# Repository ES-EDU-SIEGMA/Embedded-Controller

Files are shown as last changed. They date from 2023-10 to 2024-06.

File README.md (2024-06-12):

# Drink Mixing Machine Controller

This repository provides the source code for the RP2040 based stepper driver controller.
Further documentation of the hardware can be found in
the [main](https://git.uni-due.de/embedded-systems/student-projects/ss23-drink-mixing-machine/main) repository.

**The main branch of this repository can be considered stable and should be working at all time.**

## Local DEV Environment

### Toolchain

Required tools for the toolchain are:

- gcc (C-Compiler)
- arm-none-eabi-gcc (ARM C-Compiler)
- CMake (Build Script Generator)
- Ninja/Make (Build Tool)

### Build with CMake

#### Genrate Build Scripts

The build scripts can be generated by executing CMake in your Terminal as follows:

```bash
cmake -B build/<profile> -DUNIT_TEST:BOOL=<ON/OFF>  -DDEBUG:BOOL=<ON/OFF> -DCMAKE_BUILD_TYPE=<Debug/MinSizeRel>
```

The profile is one of three:

- _debug_
- _release_
- _unittest_

The `UNIT_TEST` option should be _ON_ for the unit-test profile and otherwise _OFF_.

The `DEBUG` option should be _OFF_ for the release profile and otherwise _ON_ to enable enhanced debug output.

The `CMAKE_BUILD_TYPE` option should be set to _MinSizeRel_ for the final targets to flash the machine for operations,
because otherwise the application provides too much output, that disturb the Python-based control application.

#### Build Targets

The targets to flash the Tiny2040 can be built by running

```bash
cmake --build build/<profile> -j4
```

The profile is one of three:

- _debug_
- _release_
- _unit-test_

## Contribution Guidelines

The source code should be formatted according to the style specified in the [.clang-format](.clang-format) file.

There are no direct commits to the main branch allowed.
If you want to contribute source-code, feel free to open a merge request with your desired changes.

### Folder Structure

The source code for the target device can be found under [src](src).
The [integration](test/integration) folder provides you with the integration tests which also double as an example for
the usage of the provided libraries.
The unit-tests aim to be executed on the local machine/server and are implemented under [unit](test/unit).

## Troubleshooting

### Serial Communication (Debugging)

The application detects the end of a send command by searching for _EOL_ (0x0A) or `\n`.
This character is not on the standard keyboard!
In minicom, for example, it can be sent with `CTRL+J`.

### Stepper Driver not working

Try with Arduino mega with example code from the TMC2209 library each stepper driver.
If the stepper driver is still not working, test after taking each of those steps:

- Check each connection
- Make sure TX and RX are correctly wired
- Use multiple different stepper drivers
- Use different USB cable to connect your computer
- Replace resistors
- Try with a different computer

If it works with the Arduino, the connections are all correct.
Try again with the pico.
If it does not work:

- Replace the pico
- Use different cable to connect your computer
- Use a different computer

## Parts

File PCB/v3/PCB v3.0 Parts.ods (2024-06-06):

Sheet: ORDER LIST
Part | Value | Formfactor | Required | Inventory | To Order | Seller | Part No. | Orderlink
MCU |  | TINY2040_HEADER | 5 | 0 | 5 | Digikey | 1778-PIM558-ND | https://www.digikey.de/short/qmt8ppf7
TMC Silentstepstick |  | TMC2209_SILENTSTEPSTICK | 20 | 8 | 12 | Mouser | 700-TMC2209SILENTSTE | https://www.digikey.de/short/qmt8ppf7 (https://mou.sr/486m3fp)
Base for Fuse |  | 4628 | 15 | 0 | 15 | Mouser | 534-4628 | https://mou.sr/3Nxg76M
Electronic Catridge Fuse |  | Cylindircal | 5 | 5 | 0
Motor Catridge Fuse | 35W @ 24V | Cylindircal | 5 | 5 | 0
TVS Diode 3V3 | PTVS3V3S1UR | PTVS3V3S1UR | 5 | 0 | 5 | Mouser | 771-PTVS3V3S1UR115 | https://mou.sr/3NCS0no
TVS Diode 5V0 | PTVS5V0S1UR | PTVS5V0S1UR | 5 | 0 | 5 | Mouser | 771-PTVS5V0S1UR115 | https://mou.sr/4atKc0L
TVS Diode 24V0 | PTVS24VS1UR | PTVS24VS1UR | 85 | 0 | 85 | Mouser | 771-PTVS24VS1UR115 | https://mou.sr/3xw49BO
Connector Header 2 Pin | B2B-PH-K-S(LF)(SN) | B2B-PH-K-S(LF)(SN) | 30 | 10 | 20 | Mouser | 571-292133-2 | https://mou.sr/475O9Gk
Connector Header 4 Pin | B4B-PH-K-S(LF)(SN) | B4B-PH-K-S(LF)(SN) | 30 | 10 | 20 | Mouser | 571-292133-4 | https://mou.sr/3RsRhpT
10k Ohm Resistor | 10kR | R-EU_R0805 | 25 | 25 | 0 | Mouser | 71-RCC080510K0FKEA | https://mou.sr/3R21yuH
100 Ohm Resistor | 100R +-5% | R-EU_R0805 | 5 | 5 | 0 | Mouser | 71-RCC0805100RFKEA | https://mou.sr/3RodXYk
0 Ohm Resistor | 0R | R-EU_R0805 | 25 |  | 25 | Mouser | 71-RCC08050000Z0EA | https://mou.sr/3NAsb7e

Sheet: Part List
Part | Value | Device | Package | Library
3V3_FUSE1 | 4628 | 4628 | FUSE_4628 | 4628
5V_FUSE | 4628 | 4628 | FUSE_4628 | 4628
24V_FUSE | 4628 | 4628 | FUSE_4628 | 4628
CONTROLLER | TINY2040_HEADER | TINY2040_HEADER | TINY2040_HEADER | tiny2040_headerd
D1 | PTVS3V3S1UR | PTVS3V3S1UR | TVS_PTVS3V3S1UR | PTVS3V3S1UR
D2 | PTVS5V0S1UR | PTVS5V0S1UR | TVS_PTVS5V0S1UR | PTVS5V0S1UR
D3 | PTVS24VS1UR | PTVS24VS1UR | TVS_PTVS24VS1UR | PTVS24VS1UR
D4 | PTVS24VS1UR | PTVS24VS1UR | TVS_PTVS24VS1UR | PTVS24VS1UR
D5 | PTVS24VS1UR | PTVS24VS1UR | TVS_PTVS24VS1UR | PTVS24VS1UR
D6 | PTVS24VS1UR | PTVS24VS1UR | TVS_PTVS24VS1UR | PTVS24VS1UR
D7 | PTVS24VS1UR | PTVS24VS1UR | TVS_PTVS24VS1UR | PTVS24VS1UR
D8 | PTVS24VS1UR | PTVS24VS1UR | TVS_PTVS24VS1UR | PTVS24VS1UR
D9 | PTVS24VS1UR | PTVS24VS1UR | TVS_PTVS24VS1UR | PTVS24VS1UR
D10 | PTVS24VS1UR | PTVS24VS1UR | TVS_PTVS24VS1UR | PTVS24VS1UR
D11 | PTVS24VS1UR | PTVS24VS1UR | TVS_PTVS24VS1UR | PTVS24VS1UR
D12 | PTVS24VS1UR | PTVS24VS1UR | TVS_PTVS24VS1UR | PTVS24VS1UR
D13 | PTVS24VS1UR | PTVS24VS1UR | TVS_PTVS24VS1UR | PTVS24VS1UR
D14 | PTVS24VS1UR | PTVS24VS1UR | TVS_PTVS24VS1UR | PTVS24VS1UR
D15 | PTVS24VS1UR | PTVS24VS1UR | TVS_PTVS24VS1UR | PTVS24VS1UR
D16 | PTVS24VS1UR | PTVS24VS1UR | TVS_PTVS24VS1UR | PTVS24VS1UR
D17 | PTVS24VS1UR | PTVS24VS1UR | TVS_PTVS24VS1UR | PTVS24VS1UR
D18 | PTVS24VS1UR | PTVS24VS1UR | TVS_PTVS24VS1UR | PTVS24VS1UR
D19 | PTVS24VS1UR | PTVS24VS1UR | TVS_PTVS24VS1UR | PTVS24VS1UR
LED | B2B-PH-K-S(LF)(SN) | B2B-PH-K-S(LF)(SN) | JST_B2B-PH-K-S(LF)(SN) | B2B-PH-K-S_LF__SN_
M1 | B4B-PH-K-S(LF)(SN) | B4B-PH-K-S(LF)(SN) | JST_B4B-PH-K-S(LF)(SN) | B4B-PH-K-S_LF__SN_
M1_TMC | TMC2209_SILENTSTEPSTICK | TMC2209_SILENTSTEPSTICK | MODULE_TMC2209_SILENTSTEPSTICK | TMC2209_SILENTSTEPSTICK
M2 | B4B-PH-K-S(LF)(SN) | B4B-PH-K-S(LF)(SN) | JST_B4B-PH-K-S(LF)(SN) | B4B-PH-K-S_LF__SN_
M2_TMC | TMC2209_SILENTSTEPSTICK | TMC2209_SILENTSTEPSTICK | MODULE_TMC2209_SILENTSTEPSTICK | TMC2209_SILENTSTEPSTICK
M3 | B4B-PH-K-S(LF)(SN) | B4B-PH-K-S(LF)(SN) | JST_B4B-PH-K-S(LF)(SN) | B4B-PH-K-S_LF__SN_
M3_TMC | TMC2209_SILENTSTEPSTICK | TMC2209_SILENTSTEPSTICK | MODULE_TMC2209_SILENTSTEPSTICK | TMC2209_SILENTSTEPSTICK
M4 | B4B-PH-K-S(LF)(SN) | B4B-PH-K-S(LF)(SN) | JST_B4B-PH-K-S(LF)(SN) | B4B-PH-K-S_LF__SN_
M4_TMC | TMC2209_SILENTSTEPSTICK | TMC2209_SILENTSTEPSTICK | MODULE_TMC2209_SILENTSTEPSTICK | TMC2209_SILENTSTEPSTICK
POWER_CONNECTOR | B4B-PH-K-S(LF)(SN) | B4B-PH-K-S(LF)(SN) | JST_B4B-PH-K-S(LF)(SN) | B4B-PH-K-S_LF__SN_
R1 | 10kR | R-EU_R0805 | R0805 | rcl
R2 | 10kR | R-EU_R0805 | R0805 | rcl
R3 | 10kR | R-EU_R0805 | R0805 | rcl
R4 | 10kR | R-EU_R0805 | R0805 | rcl
R5 | 10kR | R-EU_R0805 | R0805 | rcl
R6 | 100R +-5% | R-EU_R0805 | R0805 | rcl
R7 | 0R | R-EU_R0805 | R0805 | rcl
R8 | 0R | R-EU_R0805 | R0805 | rcl
R9 | 0R | R-EU_R0805 | R0805 | rcl
R10 | 0R | R-EU_R0805 | R0805 | rcl
R11 | 0R | R-EU_R0805 | R0805 | rcl
S1 | B2B-PH-K-S(LF)(SN) | B2B-PH-K-S(LF)(SN) | JST_B2B-PH-K-S(LF)(SN) | B2B-PH-K-S_LF__SN_
S2 | B2B-PH-K-S(LF)(SN) | B2B-PH-K-S(LF)(SN) | JST_B2B-PH-K-S(LF)(SN) | B2B-PH-K-S_LF__SN_
S3 | B2B-PH-K-S(LF)(SN) | B2B-PH-K-S(LF)(SN) | JST_B2B-PH-K-S(LF)(SN) | B2B-PH-K-S_LF__SN_
S4 | B2B-PH-K-S(LF)(SN) | B2B-PH-K-S(LF)(SN) | JST_B2B-PH-K-S(LF)(SN) | B2B-PH-K-S_LF__SN_
SPI_I2C | B4B-PH-K-S(LF)(SN) | B4B-PH-K-S(LF)(SN) | JST_B4B-PH-K-S(LF)(SN) | B4B-PH-K-S_LF__SN_
UART_1 | B2B-PH-K-S(LF)(SN) | B2B-PH-K-S(LF)(SN) | JST_B2B-PH-K-S(LF)(SN) | B2B-PH-K-S_LF__SN_

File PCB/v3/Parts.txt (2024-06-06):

Partlist

Exported from controller_board.sch at 06.02.24 19:13

EAGLE Version 9.6.2 Copyright (c) 1988-2020 Autodesk, Inc.

Assembly variant: 

Part            Value                   Device                  Package                        Library                 Sheet

3V3_FUSE1       4628                    4628                    FUSE_4628                      4628                    1
5V_FUSE         4628                    4628                    FUSE_4628                      4628                    1
24V_FUSE        4628                    4628                    FUSE_4628                      4628                    1
CONTROLLER      TINY2040_HEADER         TINY2040_HEADER         TINY2040_HEADER                tiny2040_headerd        1
D1              PTVS3V3S1UR             PTVS3V3S1UR             TVS_PTVS3V3S1UR                PTVS3V3S1UR             1
D2              PTVS5V0S1UR             PTVS5V0S1UR             TVS_PTVS5V0S1UR                PTVS5V0S1UR             1
D3              PTVS24VS1UR             PTVS24VS1UR             TVS_PTVS24VS1UR                PTVS24VS1UR             1
D4              PTVS24VS1UR             PTVS24VS1UR             TVS_PTVS24VS1UR                PTVS24VS1UR             1
D5              PTVS24VS1UR             PTVS24VS1UR             TVS_PTVS24VS1UR                PTVS24VS1UR             1
D6              PTVS24VS1UR             PTVS24VS1UR             TVS_PTVS24VS1UR                PTVS24VS1UR             1
D7              PTVS24VS1UR             PTVS24VS1UR             TVS_PTVS24VS1UR                PTVS24VS1UR             1
D8              PTVS24VS1UR             PTVS24VS1UR             TVS_PTVS24VS1UR                PTVS24VS1UR             1
D9              PTVS24VS1UR             PTVS24VS1UR             TVS_PTVS24VS1UR                PTVS24VS1UR             1
D10             PTVS24VS1UR             PTVS24VS1UR             TVS_PTVS24VS1UR                PTVS24VS1UR             1
D11             PTVS24VS1UR             PTVS24VS1UR             TVS_PTVS24VS1UR                PTVS24VS1UR             1
D12             PTVS24VS1UR             PTVS24VS1UR             TVS_PTVS24VS1UR                PTVS24VS1UR             1
D13             PTVS24VS1UR             PTVS24VS1UR             TVS_PTVS24VS1UR                PTVS24VS1UR             1
D14             PTVS24VS1UR             PTVS24VS1UR             TVS_PTVS24VS1UR                PTVS24VS1UR             1
D15             PTVS24VS1UR             PTVS24VS1UR             TVS_PTVS24VS1UR                PTVS24VS1UR             1
D16             PTVS24VS1UR             PTVS24VS1UR             TVS_PTVS24VS1UR                PTVS24VS1UR             1
D17             PTVS24VS1UR             PTVS24VS1UR             TVS_PTVS24VS1UR                PTVS24VS1UR             1
D18             PTVS24VS1UR             PTVS24VS1UR             TVS_PTVS24VS1UR                PTVS24VS1UR             1
D19             PTVS24VS1UR             PTVS24VS1UR             TVS_PTVS24VS1UR                PTVS24VS1UR             1
LED             B2B-PH-K-S(LF)(SN)      B2B-PH-K-S(LF)(SN)      JST_B2B-PH-K-S(LF)(SN)         B2B-PH-K-S_LF__SN_      1
M1              B4B-PH-K-S(LF)(SN)      B4B-PH-K-S(LF)(SN)      JST_B4B-PH-K-S(LF)(SN)         B4B-PH-K-S_LF__SN_      1
M1_TMC          TMC2209_SILENTSTEPSTICK TMC2209_SILENTSTEPSTICK MODULE_TMC2209_SILENTSTEPSTICK TMC2209_SILENTSTEPSTICK 1
M2              B4B-PH-K-S(LF)(SN)      B4B-PH-K-S(LF)(SN)      JST_B4B-PH-K-S(LF)(SN)         B4B-PH-K-S_LF__SN_      1
M2_TMC          TMC2209_SILENTSTEPSTICK TMC2209_SILENTSTEPSTICK MODULE_TMC2209_SILENTSTEPSTICK TMC2209_SILENTSTEPSTICK 1
M3              B4B-PH-K-S(LF)(SN)      B4B-PH-K-S(LF)(SN)      JST_B4B-PH-K-S(LF)(SN)         B4B-PH-K-S_LF__SN_      1
M3_TMC          TMC2209_SILENTSTEPSTICK TMC2209_SILENTSTEPSTICK MODULE_TMC2209_SILENTSTEPSTICK TMC2209_SILENTSTEPSTICK 1
M4              B4B-PH-K-S(LF)(SN)      B4B-PH-K-S(LF)(SN)      JST_B4B-PH-K-S(LF)(SN)         B4B-PH-K-S_LF__SN_      1
M4_TMC          TMC2209_SILENTSTEPSTICK TMC2209_SILENTSTEPSTICK MODULE_TMC2209_SILENTSTEPSTICK TMC2209_SILENTSTEPSTICK 1
POWER_CONNECTOR B4B-PH-K-S(LF)(SN)      B4B-PH-K-S(LF)(SN)      JST_B4B-PH-K-S(LF)(SN)         B4B-PH-K-S_LF__SN_      1
R1              270R                    R-EU_R0805              R0805                          rcl                     1
R2              10kR                    R-EU_R0805              R0805                          rcl                     1
R3              10kR                    R-EU_R0805              R0805                          rcl                     1
R4              10kR                    R-EU_R0805              R0805                          rcl                     1
R5              10kR                    R-EU_R0805              R0805                          rcl                     1
R6              100R +-5%               R-EU_R0805              R0805                          rcl                     1
R7              0R                      R-EU_R0805              R0805                          rcl                     1
R8              0R                      R-EU_R0805              R0805                          rcl                     1
R9              0R                      R-EU_R0805              R0805                          rcl                     1
R10             0R                      R-EU_R0805              R0805                          rcl                     1
R11             0R                      R-EU_R0805              R0805                          rcl                     1
S1              B2B-PH-K-S(LF)(SN)      B2B-PH-K-S(LF)(SN)      JST_B2B-PH-K-S(LF)(SN)         B2B-PH-K-S_LF__SN_      1
S2              B2B-PH-K-S(LF)(SN)      B2B-PH-K-S(LF)(SN)      JST_B2B-PH-K-S(LF)(SN)         B2B-PH-K-S_LF__SN_      1
S3              B2B-PH-K-S(LF)(SN)      B2B-PH-K-S(LF)(SN)      JST_B2B-PH-K-S(LF)(SN)         B2B-PH-K-S_LF__SN_      1
S4              B2B-PH-K-S(LF)(SN)      B2B-PH-K-S(LF)(SN)      JST_B2B-PH-K-S(LF)(SN)         B2B-PH-K-S_LF__SN_      1
SPI_I2C         B4B-PH-K-S(LF)(SN)      B4B-PH-K-S(LF)(SN)      JST_B4B-PH-K-S(LF)(SN)         B4B-PH-K-S_LF__SN_      1
UART_1          B2B-PH-K-S(LF)(SN)      B2B-PH-K-S(LF)(SN)      JST_B2B-PH-K-S(LF)(SN)         B2B-PH-K-S_LF__SN_      1

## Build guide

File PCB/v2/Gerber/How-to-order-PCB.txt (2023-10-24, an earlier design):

How to Order PCB

Please refer to:
https://docs.easyeda.com/en/PCB/Order-PCB

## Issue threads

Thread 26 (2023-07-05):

Mount Display in front panel

DavidFederl, 2023-07-05:
## Description

Install the newly delivered parts into the machine. This includes making an improved version of the display fixation in the front cover.

## Related User Stories

- [Cleaning](https://github.com/orgs/ES-EDU-SIEGMA/projects/1/views/1?pane=issue&itemId=29365987)
- [60 Seconds to drink](https://github.com/orgs/ES-EDU-SIEGMA/projects/1/views/1?pane=issue&itemId=29367077)
- [Improve UI](https://github.com/orgs/ES-EDU-SIEGMA/projects/1/views/1?pane=issue&itemId=29367221)

## ToDo

- [x] Build display mount brackets
- [ ] Add Perspex cover over display-controller and PI
- [x] Install Components into Front Cover of the machine

DavidFederl, 2023-11-24:
Required extra tools:
- [Gewindeeinsatz](https://www.amazon.de/Turmberg3D-L%C3%B6tkolben-Einschmelzhilfe-Gewindeeins%C3%A4tze-Einschmelzmuttern/dp/B09NYLSKPY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)
- [Einschmelzhilfe](https://www.amazon.de/Turmberg3D-L%C3%B6tkolben-Einschmelzhilfe-Gewindeeins%C3%A4tze-Einschmelzmuttern/dp/B097RR1KCB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)
- [M3 Schraubensortiment](https://www.amazon.de/joyan-Schrauben-Innensechskant-Innensechskantschrauben-Linsenkopfschrauben/dp/B09NDPH4RN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)

DavidFederl, 2024-01-22:
Only need to add cutouts to perspex cover!

Closed 2024-01-28.

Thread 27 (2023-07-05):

Replace Wireing

DavidFederl, 2023-07-05:
## Description

Replace old wires.

## Related User Stories

## ToDo

- [x] Sensors Right Side
- [x] LED Rondell
- [x] Power Connectors

DavidFederl, 2023-11-22:
- Cable for Data Transmission: [Twisted Shielded Pair](https://www.amazon.de/Flexibilit%C3%A4t-biegebest%C3%A4ndig-Schleppkette-Twisted-Pair-abgeschirmtes/dp/B0C1K9RLN6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)
- Cable for Motor: [4 Wires](https://www.amazon.de/CARLITS-Verl%C3%A4ngerungs-4x0-3mm%C2%B2-Leuchten-Streifen/dp/B08F3HTNKR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)
- Cable for sensor: [2 Wires](https://www.amazon.de/CARLITS-2x0-32mm%C2%B2-Verzinntes-Kabelanschluss-Elektrischer/dp/B088NWL5RL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)

---

We are required to order Cable with 2 wires, because we need to redo the sensor wireing and LED wireing!

DavidFederl, 2024-01-22:
WAITING FOR: female pcb connectors

DavidFederl, 2024-01-25:
Parts arrived!

Closed 2024-02-07.

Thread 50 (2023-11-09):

Prepare a draft for interfaces for dispenser/motor libs

glencoe, 2023-11-09:
What are the problems with these libs at the moment?
How should the new interfaces look like to fix these issues?
What are functions and function signatures for each of these libs?
What is the expected behaviour for these functions?

Finally discuss the draft in the group and finalize the interfaces.

HuangQing23, 2023-11-21:
Some questions from last week
1.Why we use dispenser Emergency stop?
We just use it for testing. It should not be in the public version.

2.Should motor get the time we calculate or just execute the command we preseted in the code?

3.In motor lib, function setUpEnablePin,
MOTOR_ENABLE_PINT_0-->2
MOTOR_ENABLE_PINT_1-->3
MOTOR_ENABLE_PINT_2-->6
MOTOR_ENABLE_PINT_3-->7
In the datasheet and pcb design we can see that, 2-->6 and 3-->7 is correct, but why the function still work when
MOTOR_ENABLE_PINT_0-->2
MOTOR_ENABLE_PINT_1-->3
when it should be MOTOR_ENABLE_PINT_0-->4 and MOTOR_ENABLE_PINT_1-->5?

HuangQing23, 2023-11-22:
In motor :
1.We can change motor_t --> Motor_Entity or ?
2.For these two functions 'enableMotorByPin' and 'disableMotorByPin',we can wrap these two functions into one
3.Shall we delete function'motorIsCommunicating' cause we can just use TMC2209_isSetupAndCommunicating(&motor->tmc2209) instead or we can use an explanatory variable like 'communicationState'
4.We should delete the repetitive parts of  'moveMotorUp', 'moveMotorDown', 'stopMotor'
5.Maybe we should change the names of TMC2209_moveAtVelocity, cause it's used for 'stopMotor'

In dispenser :
for 'dispenserStateCode_t dispenserGetStateCode':
1.shall we change dispenserGetStateCode-->getDispenserState
2.delete the 'else', keep the 'if' to reduce nesting

for 'dispenserEmergencyStop':
1.We should delete it in the public version

for 'resetDispenserPosition':
1.I think we should do something in the while loop to make sure if limitswitch broken then we can stop or avoid a crisis
(when we can use torque or something to get a exact position for reset,we shall delete this function or change it )

for 'dispenserSetAllToSleepState':
we better change it to 'dispenserAllInSleepState'

also for 'dispenserState_t upState(dispenser_t *dispenser)':
we should pay attention to this code segment----
if (!limitSwitchIsClosed(dispenser->limitSwitch)) {
        dispenser->stepsDone++;
    }

In rondell :
1. We can change createRondell -->setUpRondell, in view of the code in motor. And change setUpRondell -->createRondell

In left_controller library and rondell controller :
1. We should put both 'initHardware(false)' and 'establishConnectionWithController("LEFT")' out of the main function.
So we can write a function in helper that conclude both these two funtions.
(Shall we also put in the watchdog?)
2. There are different 'initDispenser' in left_controller and rondell controller , we should separate them

HuangQing23, 2023-11-22:
We should change the code in 'handleMessage' or 'if (isLineEnd(input))' to solve the situation when we want to swtich to another controller

HuangQing23, 2023-12-01:
1.Did some renaming to make the function more readable.
2.Moved the states and motorDoStep(used to be dispenserDoStep) and dispenserAllInSleepState from dispenser library to motor library and fix the headers.
3.Write a function for 'calibrated' to make sure 'initDispenser()' and 'initRondellDispenser()' is successful. But it seems better to move it to dispenser later.
4.Add a function 'isIdentifier' in helper(handleMessage) for switch to another controller, but based on some size problem it need some more changes, but it's ok if we don't enter words except 'i'.
5.Tried to change the function 'motorIsCommunicating(Motor_t *motor)' but it seems some problems happened. We can discuss it later.

HuangQing23, 2023-12-01:
Should do cleaner separations for the structure of dispenser and motor.

HuangQing23, 2023-12-01:
Due to some medical condition I delayed this commit then I clicked the wrong button which made task 49 create its own branch so I had to link the branch to this task first but it seems like my account can't solve this problem.

YULEMING, 2023-12-05:
Have you built the `left` successfully, I tried but failed on branch [refactoring the code](https://github.com/ES-EDU-SIEGMA/Embedded-Controller/tree/refactoring-the-code).

HuangQing23, 2023-12-05:
> Have you built the `left` successfully, I tried but failed on branch [refactoring the code](https://github.com/ES-EDU-SIEGMA/Embedded-Controller/tree/refactoring-the-code).

Yeah I built it without reporting an error. But I will check again.

Closed 2024-01-09.

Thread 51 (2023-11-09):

Research if TMC provides advanced functionality

DavidFederl, 2023-11-09:
Check if the TMC SilentStepKick provides additional functionality like an stop if a torque limit is reached and if multiple steps can be done with one command.

YULEMING, 2023-11-12:
We are using:
* TMC2209 V1.2 from BIGTREETECH, here is a simplified manual from BIGTREETECH: [TMC2209-V1.2-manual.pdf](https://github.com/bigtreetech/BIGTREETECH-TMC2209-V1.2/blob/master/manual/TMC2209-V1.2-manual.pdf).
* Usongshine 17HS4401 motor: See our Documentation/datasheets/[Motor-17HS4401.pdf](https://github.com/ES-EDU-SIEGMA/Documentation/blob/main/datasheets/Motor-17HS4401.pdf)

**For your convenience**
17HS4401 Electrical Specifications:
|Step Angel (deg)|Motor Length (mm)|Rated Current (A)|Phase Resistance (ohm)|Phase Inductance (mH)|Holding Torque (N.cm Min)|Detent Torque (N.cm Max)|Rotor Inertia (g.cm<sup>2</sup>)|Lead Wired (No.)|Motor Weight (g)|
|-|-|-|-|-|-|-|-|-|-|
|1.8|40|1.7|1.5|2.8|40|2.2|54|4|280|

May it helps.

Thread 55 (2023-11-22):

New implementation of time to hold top position.

kamilloo1, 2023-11-22:
Because we made measuring torque faster in [this ](https://github.com/ES-EDU-SIEGMA/Embedded-Controller/issues/41) issue, the time to hold the top position needs to be recalculated and implemented.

YULEMING, 2023-11-28:
The current `dispenser` has an attribute `haltSteps`. It is used in topState to control the time that the dispenser stops at the top position. Because we are going to use time instead of steps, I recommend that we change `haltSteps` to `haltTime`, which means: *This dispenser is going to stop at the top position for 'haltTime' ms*. But this will influence some other dispenser functions. Details are as follows:
### File: [dispenser.h](https://github.com/ES-EDU-SIEGMA/Embedded-Controller/blob/main/src/dispenser/dispenser.h#L36)
```c
struct dispenser {
    ...
    // uint16_t haltSteps;
    uint32_t haltTime;
    ...
};
```
### File: [dispenser.c](https://github.com/ES-EDU-SIEGMA/Embedded-Controller/blob/main/src/dispenser/dispenser.c)
```c
void dispenserSetHaltTime(dispenser_t *dispenser, uint32_t haltTime) {
//    dispenser->haltSteps = haltTime / DISPENSER_STEP_TIME_MS;
    // Change dispenser->haltSteps to dispenser->haltTime
    dispenser->haltTime = haltTime;
    // PRINT_DEBUG("Dispenser %u will stop after %hu steps", dispenser->address, dispenser->haltSteps)
}
```
```c
void dispenserCreate(dispenser_t *dispenser, SerialAddress_t address, serialUart_t uart,
                     uint8_t dispenserCL, uint16_t searchTimeout) {
    ...
    // dispenser->haltSteps = 0;
    dispenser->haltTime = 0;
    ...
}
```
```c
void dispenserEmergencyStop(dispenser_t *dispenser) {
    ...
    // dispenser->haltSteps = 0;
    dispenserSetHaltTime(dispenser, 0);
    ...
}
```
* `haltTime` would be assigned every time when it needs to work, but it would be stable if we set it to 0. E.g. what if we say: *Let all dispensers start to work as long as its `haltTime` is not 0?* But that dispenser stopped last time without setting `haltTime` to 0?
```c
static dispenserState_t errorState(dispenser_t *dispenser) {
    ...
    if (...)) {
        ...
        // dispenser->haltSteps = 0;
        dispenserSetHaltTime(dispenser, 0);
        ...
    }
    ...
}
```
```c
static dispenserState_t sleepState(dispenser_t *dispenser) {
//    if (dispenser->haltSteps > 0) {
//        enableMotorByPin(&dispenser->motor);
//        moveMotorUp(&dispenser->motor);
//        return upState_t;
//    }
    return sleepState_t;
}
```
* This `sleepState` will check whether the dispenser really finished or not by checking `haltSteps`. Because we use `haltTime` instead of `haltSteps`, I don't see any situation once we get into `sleepState` but the dispenser still has unfinished steps and needs to go back to `upState`. No need to do it anymore.
```c
static dispenserState_t topState(dispenser_t *dispenser) {
    PRINT_DEBUG("topState")
    // Change dispenser->haltSteps to dispenser->haltTime
    sleep_ms(dispenser->haltTime);
    dispenserSetHaltTime(dispenser, 0);
    return downState_t;
}
```
```c
static dispenserState_t downState(dispenser_t *dispenser) {
    ...
    if (...)) {
        ...
        // dispenser->haltSteps = 0;
        dispenserSetHaltTime(dispenser, 0);
        ...
    }
    ...
}
```

YULEMING, 2023-11-28:
The current `dispenser` also has attributes `stepsUp` and `stepsDown`. Because of the above changes, these two are only working as counters. We don't do any `if condition` stuff on them. We can also get rid of them.
### File: dispenser.h
```c
struct dispenser {
    ...
    // uint16_t stepsDone;
    // uint16_t stepsUp;
    // This haltSteps is used in topState, we can change it to "haltTime"
    // uint16_t haltSteps;
    uint32_t haltTime;
    ...
};
```
### File: dispenser.c
```c
void dispenserCreate(dispenser_t *dispenser, SerialAddress_t address, serialUart_t uart,
                     uint8_t dispenserCL, uint16_t searchTimeout) {
    ...
    // This haltSteps is used in topState, we can change it to "haltTime"
    // dispenser->haltSteps = 0;
    dispenser->haltTime = 0;
    // dispenser->stepsDone = 0;
    ...
}
```
```c
static dispenserState_t upState(dispenser_t *dispenser) {
    ...
    // If the torque is below 10 twice in a row, stop
    if (torque < 10){
        ...
        if (counterTorque == 2){
            ...
            // dispenser->stepsUp = dispenser->stepsDone;
            ...
        }
    }
    else ...

    if (!limitSwitchIsClosed(dispenser->limitSwitch)) {
        // dispenser->stepsDone++;
    }
    ...
}
```
```c
static dispenserState_t downState(dispenser_t *dispenser) {
    ...
    if (limitSwitchIsClosed(dispenser->limitSwitch)) {
        ...
        // dispenser->haltSteps = 0;
        dispenserSetHaltTime(dispenser, 0);
        ...
    }
    // dispenser->stepsDone++;
    ...
}
```

glencoe, 2023-11-29:
Seems reasonable. Please open a pull request that features your changes

YULEMING, 2023-12-05:
Some problems are found with the above method, and this should be continued based on the newly refactored code.

YULEMING, 2023-12-16:
Based on `develop` branch.
```c
static dispenserState_t topState(dispenser_t *dispenser) {
    PRINT_DEBUG("topState")
    if (dispenser->haltTime > 0) {
        sleep_ms(TOP_TIME_SLOT);
        dispenser->haltTime = dispenser->haltTime - TOP_TIME_SLOT;
        return topState_t;
    }
    // reset to 0 when change to down state.
    dispenserSetHaltTime(dispenser, 0);
    moveMotorDown(&dispenser->motor);
    return downState_t;
}
```
The `TOP_TIME_SLOT` is defined as 1. Assume command `100;\n` is sent. Dispenser will sleep 1ms at the top position 100 times. If dispenser sleeps 100ms at the top position 1 time, others will have to wait 100ms.
```c
static dispenserState_t sleepState(dispenser_t *dispenser) {
    if (dispenser->haltTime > 0) {
        enableMotorByPin(&dispenser->motor);
        moveMotorUp(&dispenser->motor);
        return upState_t;
    }
    return sleepState_t;
}
```
`sleepState` will check `haltTime` instead of `haltSteps`.

#### When the refactoring is finished, I will implement the changes in new code.

YULEMING, 2024-01-15:
Make sense. Thank you for telling me that.
1. When I was doing the task: measure the torque more frequently, there was a situation that when all 4 dispensers are working, when no sleep in the end of `TMC2209_read`, 2 of 4 dispensers won't stop correctly. They stuck in the `upState`. But it worked well when 1 dispenser is working. According to how you sovled your #56, I think the reason is:
```c
static uint8_t counterTorque = 0;
static uint16_t torque = 0;
...
static dispenserState_t upState(dispenser_t *dispenser) {
    torque = motorGetTorque(dispenser->address);
    PRINT_DEBUG("upState")
    PRINT_DEBUG("Torque: %i", torque)

    // If the torque is below 10 twice in a row, stop
    if (torque < 10){
        counterTorque++;
        if (counterTorque == 2){
            PRINT_DEBUG("detect Top Position")
            stopMotor(dispenser->address);
            counterTorque = 0;
            return topState_t;
        }
    }
    else counterTorque = 0;
    return upState_t;
}
```
the `torque` here is a shared variable because we are using if statement. So the last counted torque is from another dispenser. I will try to make `torque` be non-shared and try to remove the `sleep` in the end of `TMC2209_read` to **reduce the cycle time**. Even if it has no influence on the cycle time, I still don't think it's a good idea to make `torque` here be shared.

2. I will measure the cycle time, figure out the relation between the input and real time, and adjust the sleep time in `topState`

YULEMING, 2024-01-15:
In the old `topState`, no sleep, only count halt steps. It's like: 1000 / 100 = 10 halt steps in total. Then just run `topState` 10 times. When I do `sleep` stuff, I have to consider other dispensers. Because 1 dispenser sleeps, it has to wait others to sleep. I think that's why there is a `othersTriggered` in the old `topState`. I think we do need an attribute to let the current dispenser know how many dispensers are working at the same time, and to reduce correct time or steps in one `topState`.

YULEMING, 2024-01-15:
Before one dispenser really runs one of the `xxxState` functions, it will still check the motor, which already spent 1ms. Same on topState. I saw the new downState function, there will be 1 or 2 times `motorGetTorque`. Tomorrow I will try to reduce the 1ms sleep at first. If we can't, here is my new thought:
1. use a shared counter variable declared in dispenser.h, so that it can be reset in the controller file and can be accessed in the dispenser.c file
2. reset in the beginning of every `do while` loop in controller file
3. after each `motorGetTorque`, counter++, so that we know how many 1ms already spent, in order to reduce the halt counter in `topState`.

YULEMING, 2024-02-19:
Find the proper method to implement the timing for topstate. #76
After fixing #84

YULEMING, 2024-02-27:
#### Important changes:
* @HuangQing23 moved motor check out of and before the do-while loop
* Running sequence in topState changed from:
    * motor check
    * dispenser run
    * motor check
    * dispenser run
    * motor check
    * dispenser run
    * motor check
    * dispenser run
* To: (motor check is done before going into this running sequence)
    * dispenser run
    * dispenser run
    * dispenser run
    * dispenser run
#### Based on the above changes
* The countdown method (without sleep): countdown by the number of dispensers now in topState from 1000 (number from the command) to 0,
    * approximate to 1000ms
    * the longer the halt time, the more significant the deviation
But in my point of view, the longest halt time should be the time that the dispenser need from full to empty. Longer halt time makes no or less sense.

YULEMING, 2024-02-27:
### Attention
* Please note that the same code spends different times in the `debug` and `release` modes because the `PRINT_DEBUG` stuff won't be counted in `release` mode.
* If the halt time is longer than the command, and there is `PRINT_DEBUG` or something like that, remove or comment relevant statement.

Closed 2024-02-28.

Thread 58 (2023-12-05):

Improve Unit Test Coverage

YULEMING, 2023-12-05:
* [x] Repair Unit Test. Fix bugs and build it successfully.
* [x] Figure out the current coverage of Unit Test.
* [ ] Extent the coverage of Unit Test.

YULEMING, 2023-12-11:
#### Repair Unit Test. Fix bugs and build it successfully.
* After fixing some naming and declaration errors, the unit-test can be built successfully now.
#### Figure out the current coverage of Unit Test.
It tests:
* dispenser
  * the structure of the dispenser (working)
  * the cycle of the dispenser (not working)

YULEMING, 2023-12-11:
### Extent the coverage of Unit Test.
Tasks list, from bottom to top, easy to hard:
* [ ] Limit switch
* [ ] Hardware helper
* [ ] serial UART
* [ ] tmc2209
* [ ] motor
* [ ] dispenser
* [ ] Rondell
* [ ] controller
* [ ] rondell controller

YULEMING, 2023-12-17:
Yes, just pushed [here](https://github.com/ES-EDU-SIEGMA/Embedded-Controller/tree/%2358-fix-improve-unit-test). But it's not finished yet. The CMakeLists.txt will keep changing and may not be able to be built directly.

DavidFederl, 2024-02-13:
Please see #81

Closed 2024-02-19.

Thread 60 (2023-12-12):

Create Gerber Files for PCB

DavidFederl, 2023-12-12:
Generate Gerber Files for new PCB design.

---

- [x] Determine required CAM configuration
- [x] Create all required Gerber files
- [x] Check if Gerber Files are valid!
- [x] Add Gerber Files to Repository (zip-archive)

DavidFederl, 2023-12-12:
CAM Files for JLCPCB can be downloaded from their [website](https://jlcpcb.com/help/article/9-How-to-Generate-Gerber-and-Drill-Files-in-Autodesk-Eagle).

---

To assure the gerber files are valid it is recommended to check them with a tool online tool like[gerblook](https://gerblook.org) or a local program like [gerbv](https://gerbv.github.io/).

Closed 2023-12-12.

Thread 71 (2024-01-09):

Assemble new PCBs

DavidFederl, 2024-01-09:
Assemble three new PCBs for the machine once all required components are delivered!

## ToDo

- PCB **LEFT**
    - [x] Assembled
    - [x] Integrated
    - [x] Tested
 - PCB **RIGHT**
    - [x] Assembled
    - [x] Integrated
    - [x] Tested
  - PCB **RONDELL**
    - [x] Assembled
    - [x] Integrated
    - [x] Tested

DavidFederl, 2024-01-22:
@YULEMING and @HuangQing23: I tested your PCBs -> one of them has faulty TVS-Diodes (I fixed them)

---

You only need to add the female headers for the TMC/Tiny modules. I would recommend using a broken TMC/Tiny to hold them in place while soldering.

YULEMING, 2024-02-02:
* With the new PCB board, it stops in the while loop:
```c
void setUpMotor(Motor_t *motor, SerialAddress_t address) {

    TMC2209_setupByMotor(&motor->tmc2209,address);

    while (!TMC2209_isSetupAndCommunicating(&motor->tmc2209)) {
        if (TMC2209_disabledByInputPin(&motor->tmc2209)) {
            PRINT_DEBUG("Setup: Stepper driver with address %u DISABLED by input pin!", address)
        }
        PRINT_DEBUG("Setup: Stepper driver with address %u NOT communicating and setup!", address)
        TMC2209_setupByMotor(&motor->tmc2209,address);
        sleep_ms(500);
    }
    ...
}
```
with this output:
`[MOTOR: setUpMotor] Setup: Stepper driver with address 0 NOT communicating and setup!.`
**The problem is there is something wrong when writing or reading register `GlobalConfig`**
**The `pdn_disable` bit is 1 in the message we write into the register, but is 0 when we read.**
* The condition of the while loop is checking register `GlobalConfig`:
```c
const static uint8_t ADDRESS_GCONF = 0x00;
typedef union GlobalConfig {
    struct {
        ...
        uint32_t pdn_disable : 1;
        ...
    };
    uint32_t bytes;
} TMC2209_GlobalConfig_t;
```
the `pdn_disable` bit. The while loop is done when this bit is `1`.
* We write this bit here:
```c
void setUpMotor(Motor_t *motor, SerialAddress_t address) {

    TMC2209_setupByMotor(&motor->tmc2209,address);

    ...
}
```
And we check `pdn_disable` right after `TMC2209_setupByMotor(...);`:
```c
void setUpMotor(Motor_t *motor, SerialAddress_t address) {

    TMC2209_setupByMotor(&motor->tmc2209,address);

    while (!TMC2209_isSetupAndCommunicating(&motor->tmc2209)) {
        ...
    }
    ...
}
```
* If `pdn_disable` is not `1`, we setup it again:
```c
void setUpMotor(Motor_t *motor, SerialAddress_t address) {

    TMC2209_setupByMotor(&motor->tmc2209,address);

    while (!TMC2209_isSetupAndCommunicating(&motor->tmc2209)) {
        ...
        TMC2209_setupByMotor(&motor->tmc2209,address);
        ...
    }
    ...
}
```
* The tmc setup `GlobalConfig` by calling `TMC2209_setOperationModeToSerial` inside `TMC2209_setup`:
```c
void TMC2209_setOperationModeToSerial(TMC2209_t *tmc2209, serialUart_t serial,
                                      long serial_baud_rate, SerialAddress_t serial_address) {
    ...
    tmc2209->global_config.pdn_disable = 1;
    ...

    TMC2209_writeStoredGlobalConfig(tmc2209);
}
```
as you can see `pdn_disable` is 1.
* Here we read the value of `pdn_disable`
```c
bool TMC2209_serialOperationMode(TMC2209_t *tmc2209) {
    TMC2209_GlobalConfig_t global_config;
    global_config.bytes = TMC2209_readGlobalConfigBytes(tmc2209);

    return global_config.pdn_disable;
}
```
the `global_config.pdn_disable` is returned again:
```c
bool TMC2209_isSetupAndCommunicating(TMC2209_t *tmc2209) {
    return TMC2209_serialOperationMode(tmc2209);
}
```
you can find it's 0 when you print the debug message.
All the `read` and `write` here are finally executed by `TMC2209_read` and `TMC2209_write`. If they worked well in the past, then there is nothing wrong with them?

* I tested the integration test of the limit switch and motor. When testing the limit switch, there is no change when I open or close the limit switch. When testing the motor, it also stops in the same while loop.

###Do you have any idea that anything might influence this?
* The new design of the PCB?
* The tmc is broken?
* The change of the enable pin in the code?
* Or something is wrong with the code, but somehow they still worked in the past?

YULEMING, 2024-02-02:
The PCB board with `1A` and `2A` labels, when testing the limit switch, no change when I close and open the limit switch.
The PCB board on the machine, all limit switches work well. The state of limit switch changed when I open and close them.
The rest PCB board, limit switch 1 and 2 work well. The limit switch 3 no state change. When I close and open limit switch 4, the states of limit switch 3 and 4 change together.
But all TMCs are not working on all 3 PCB boards.

DavidFederl, 2024-02-05:
The limitswitches are working as expected now. The TMC2209 are still not reachable. I'll try to figure it out, by checking the UART communication.

DavidFederl, 2024-02-06:
I would think the TMC2209 requires some form of adjustment to work properly. -> [FAQ for Setup](https://learn.watterott.com/de/silentstepstick/faq/#wie-stellt-man-den-motorstrom-ein)

DavidFederl, 2024-02-07:
> The limitswitches are working as expected now. The TMC2209 are still not reachable. I'll try to figure it out, by checking the UART communication.

The UART communication is working now. The resistor value was specified to large. It has to be 270Ω.

Closed 2024-02-07.

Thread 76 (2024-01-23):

Figure out 2 ways to implement the top timing

YULEMING, 2024-01-23:
1. Fix the shared variable `torque` in `upState` and try to reduce the sleep time in `TMC2209_read`.
2. If yes, implement the following:
3. Sample:
    1. INPUT: 1000;0;2000;3000; Assume each `topState` spend 1ms (in total, not really sleep 1ms in `topState`)
    2. OUTPUT:
        1. dispenser 1: 333 times run `topState`
        2. dispenser 2: 0
        3. dispenser 3: 333 + 500 times run `topState`
        4. dispenser 4: 333 + 500 + 1000 times run `topState`
4. Sample:
    1. INPUT: 1000;0;2000;2000;
    2. OUTPUT:
        1. dispenser 1: 333
        2. dispenser 2: 0
        3. dispenser 3: 333 + 500
        4. dispenser 4: 333 + 500
 5. If not, try interrupt.

YULEMING, 2024-01-23:
By changing torque to dispenser->torque, now the sleep time in TMC2209_read is 20us (>20us also works). 10us doesn't work at all, it can't even finish the initialization stage. I think the time influence of `motor-check` and `getTorque` stuff can be ignored.

YULEMING, 2024-02-04:
Method 3, TODOs:
1. remove sleep in topState and test the time consumption of topState.
2. use a common variable to let dispenser working in topState make a proper countdown.
3. then add sleep with proper time to let dispenser halt for a certain time.

Closed 2024-02-19.

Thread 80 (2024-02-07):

adjust TMC2209 to perform correctly

DavidFederl, 2024-02-07:
> I would think the TMC2209 requires some form of adjustment to work properly. -> [FAQ for Setup](https://learn.watterott.com/de/silentstepstick/faq/#wie-stellt-man-den-motorstrom-ein)

 _Originally posted by @DavidFederl in [#71](https://github.com/ES-EDU-SIEGMA/Embedded-Controller/issues/71#issuecomment-1930438760)_

YULEMING, 2024-02-07:
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

So the `A` and `B` of the motor are like this, but I don't know which one is A or B on the motor.
But the motor 04 on the `Left` is working well, so I moved it's connector from `M4` to `M1` and it also worked well.
The `M4` is closer to the TINY than `M1`, so I moved the connector of motor 01 from `M1` to `M4` but it still didn't work well. In this case, the cables' order is the same as motor 04.
Then I changed the order of the colored cables but none of them worked as well as motor 04.

I also exchanged the position of TMC2209 of `M4` and `M1`, but it also didn't work.

On the TMC2209 there are A1 and A2, I'm also not sure which one is A.

Might this have anything to do with the problem now on TMC2209?

DavidFederl, 2024-02-07:
The A B coils of the motor are provided with a current through the TMC2209. This current is generated by a PWM so that the motor is running smoothly.
To my point of view the TMC2209 needs to be adjusted so that the output current is set correct, like mentioned [in this guide](https://learn.watterott.com/de/silentstepstick/faq/#wie-stellt-man-den-motorstrom-ein). I would checking this by comparing a TMC2209 that is working correctly and comparing it to one not working.

DavidFederl, 2024-02-09:
Measure the current between GND and V_Ref Pin on a working TMC2209 and compare it to the non working TMC2209. If there is a difference adjust the Potentiometer to get the value measured on the working TMC2209.

DavidFederl, 2024-02-13:
# The hardware is now working as expected.

## Fixed Problems

- The tiny2040 were flashed with the wrong version of the integration test. => **Build from develop branch for now!**
- The Crimp contacts for one the motor cables failed which caused problems. => **Replaced the faulty parts**

Closed 2024-02-13.

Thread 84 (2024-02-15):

Fix the problem when testing left/rondell/right

HuangQing23, 2024-02-15:
When we use USB to connect three pcb boards to test left/rondell/right, it always stops at the execution to output  "moveDown" in 'PRINT_DEBUG("moveDown")' of 'resetDispenserPosition(dispenser_t *dispenser)'. Function 'moveMotorDown' was executed but it seems like the motors are not running.

YULEMING, 2024-02-19:
* Yes, and by integrationTest_Motor it calls the same function `moveMotorDown` but it works.
Due to it doesn't work in `resetDispenserPosition` `debug` `left`, it sticks in the following while loop:
```c
static void resetDispenserPosition(dispenser_t *dispenser) {
    ...
    moveMotorDown(dispenser->address);
    PRINT_DEBUG("moveDown")
    while (!limitSwitchIsClosed(dispenser->limitSwitch))
        ;
    ...
```
* So the question is: why `moveMotorDown` works in `integrationTest_motor` `debug`, but not in `resetDispenserPosition` `debug` `left`?
* I don't think `moveMotorUp` and `stopMotor` will either work in `resetDispenserPosition` `debug` `left`.

HuangQing23, 2024-02-20:
fix the problem by #85

HuangQing23, 2024-02-20:
To make the motors work  properly, we should get the rope wrapped clockwise around the motor's rotating shaft. This is because our function 'moveMotorDowm' will make the motor shaft rotates clockwise. If the rope is wrapped in the opposite direction of the motor shaft rotation due to rope length or over-rotation of the shaft, then the input command will rotate in the opposite direction of the actual rotation.

Closed 2024-02-21.

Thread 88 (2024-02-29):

Pass velocity for motor to setUp function

kamilloo1, 2024-02-29:
Because the rotation of the rondell requires a slower speed then the moving up of the lever of the dispenser, we need the motors to operate at two different speeds. The Dispenser requires a higher speed to make the torque detection work.
**Right now the velocity to the motor is passed via `#define` which affects the motor speed for all use cases.** To solve the problem, the velocity for the motor should be set via variables during setUp and stored inside the struct that holds the motor configuration!

DavidFederl, 2024-06-10:
See #102

Closed 2024-06-10.

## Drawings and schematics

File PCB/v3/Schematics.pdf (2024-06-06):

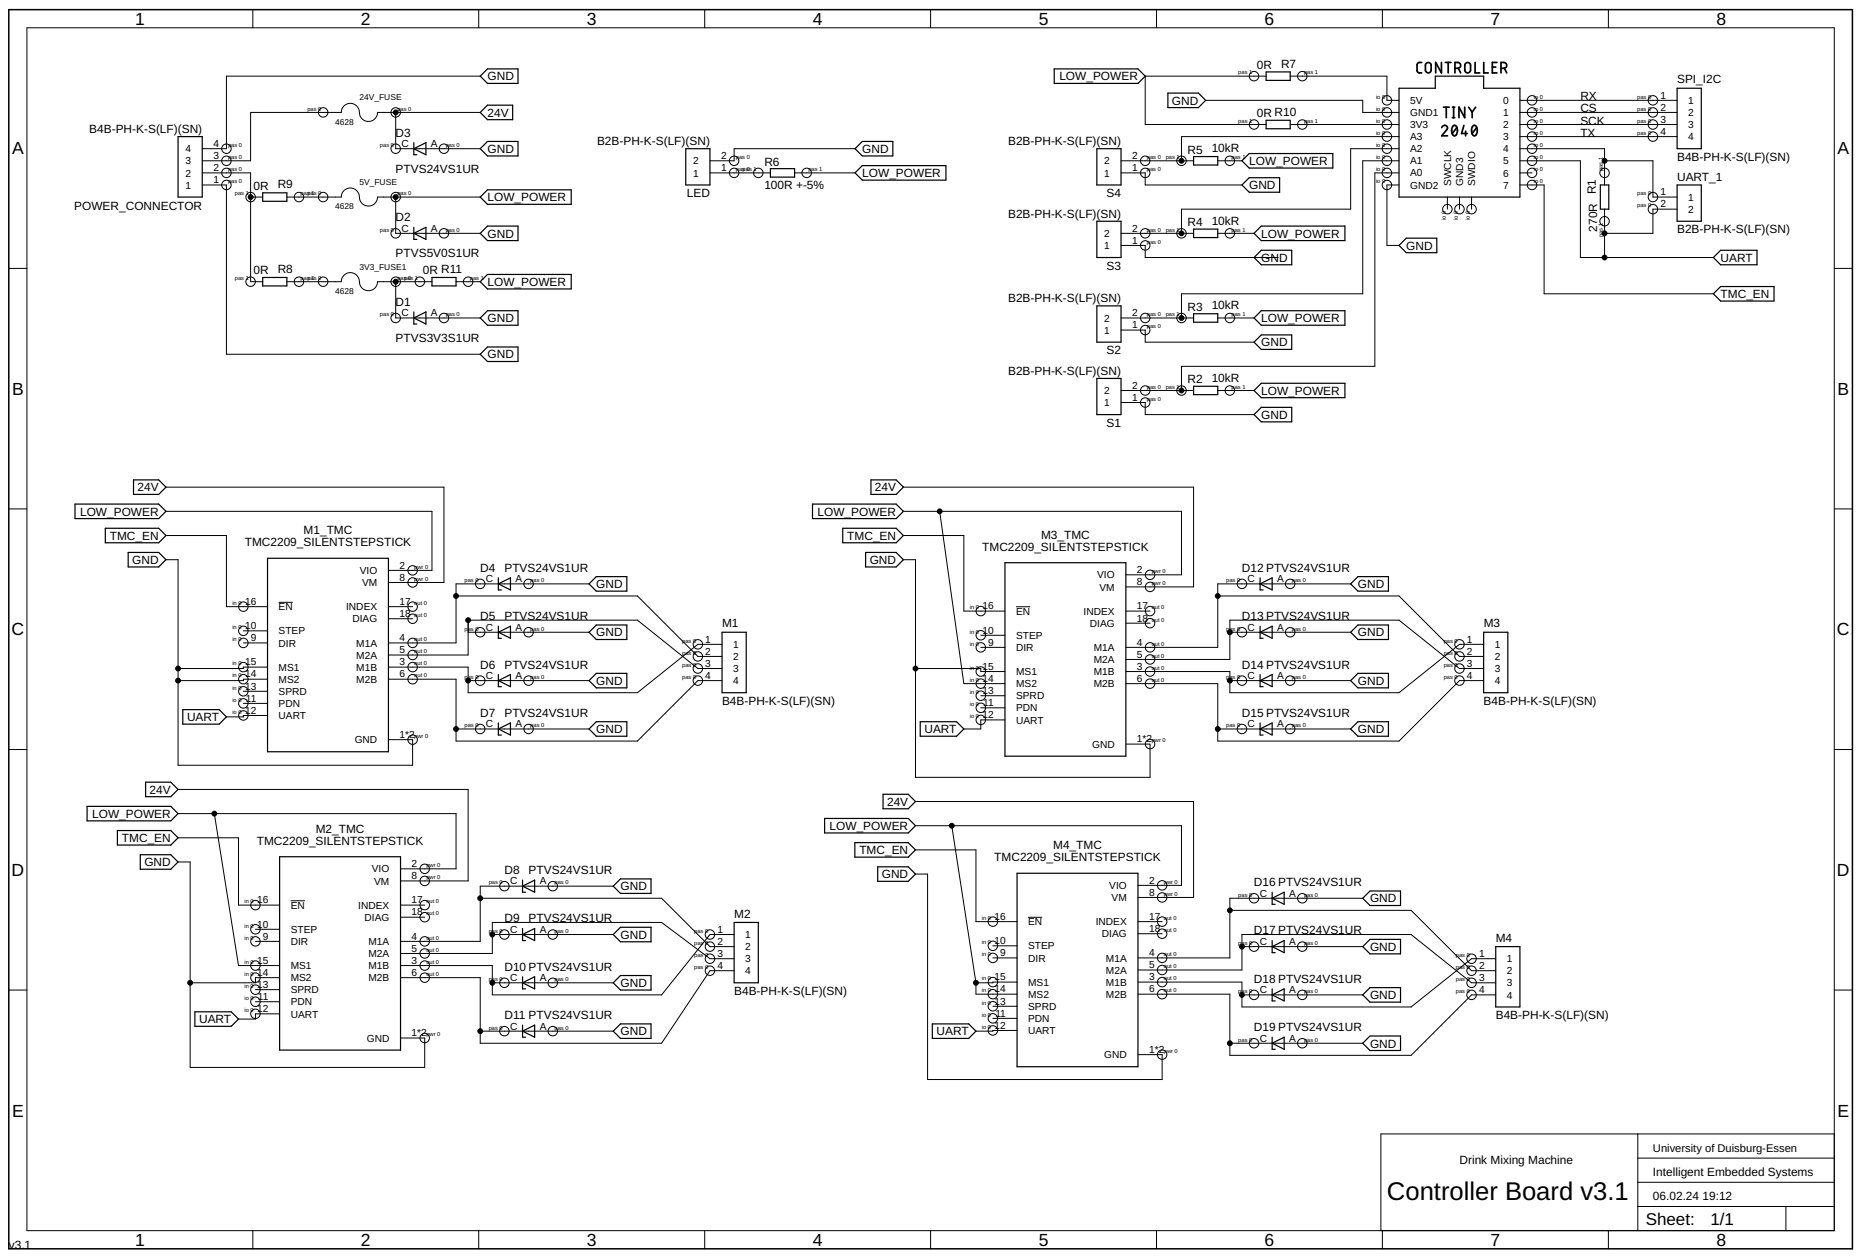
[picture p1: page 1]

Intelligent Embedded Systems University of Duisburg-Essen 06.02.24 19:12

Drink Mixing Machine Controller Board v3.1

Sheet: 1/1

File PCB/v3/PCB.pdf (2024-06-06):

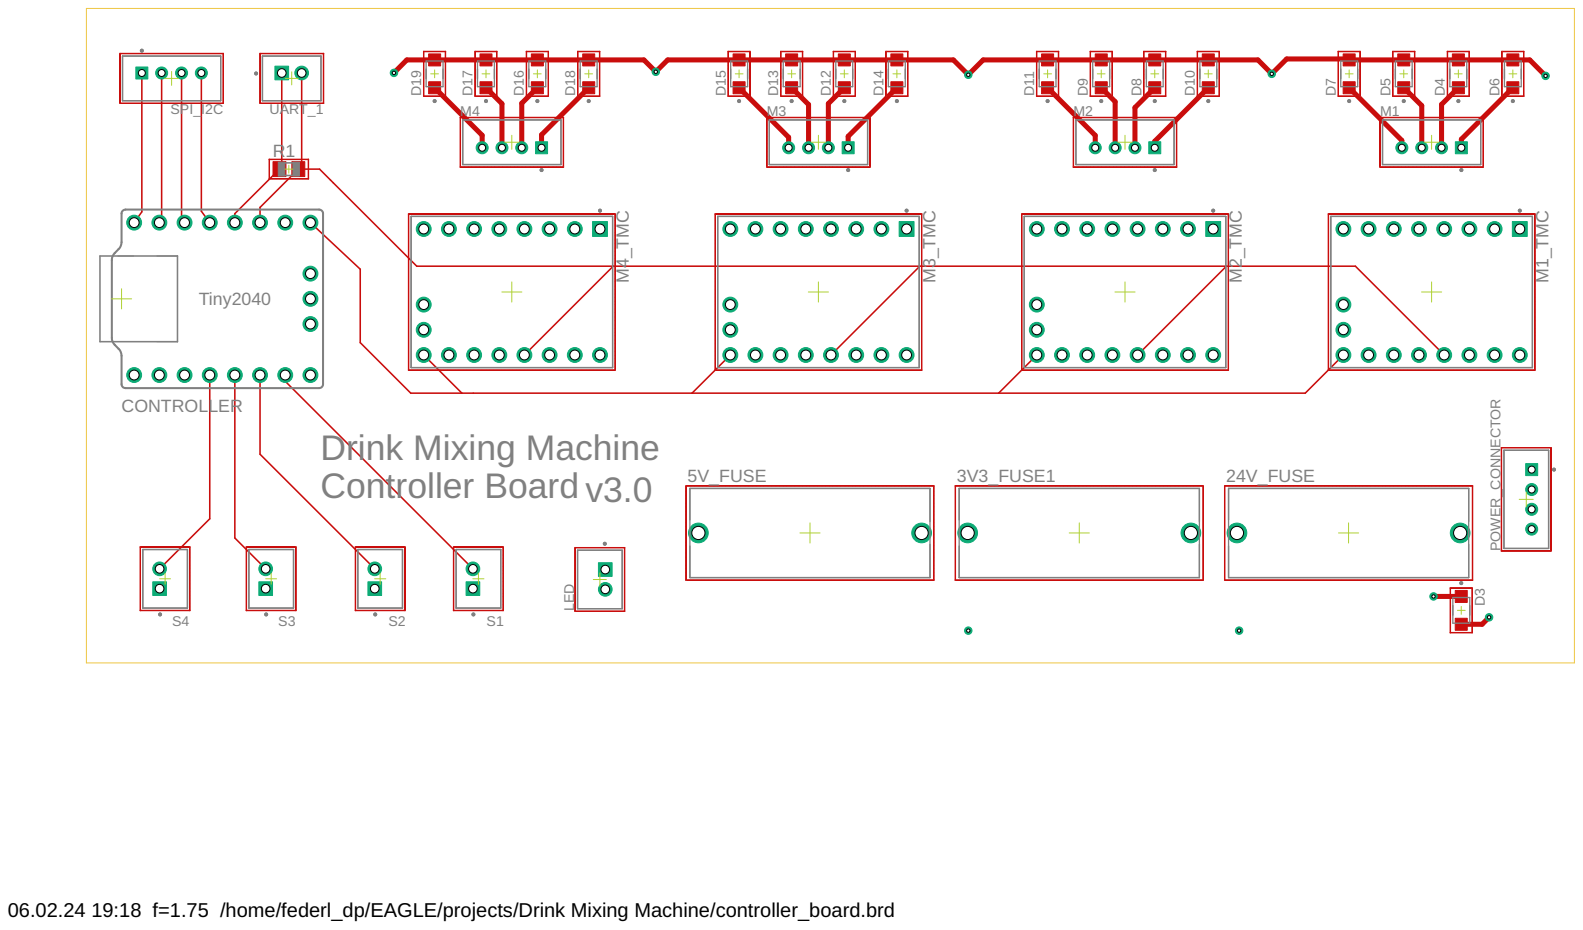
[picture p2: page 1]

06.02.24 19:18 f=1.75 /home/federl_dp/EAGLE/projects/Drink Mixing Machine/controller_board.brd

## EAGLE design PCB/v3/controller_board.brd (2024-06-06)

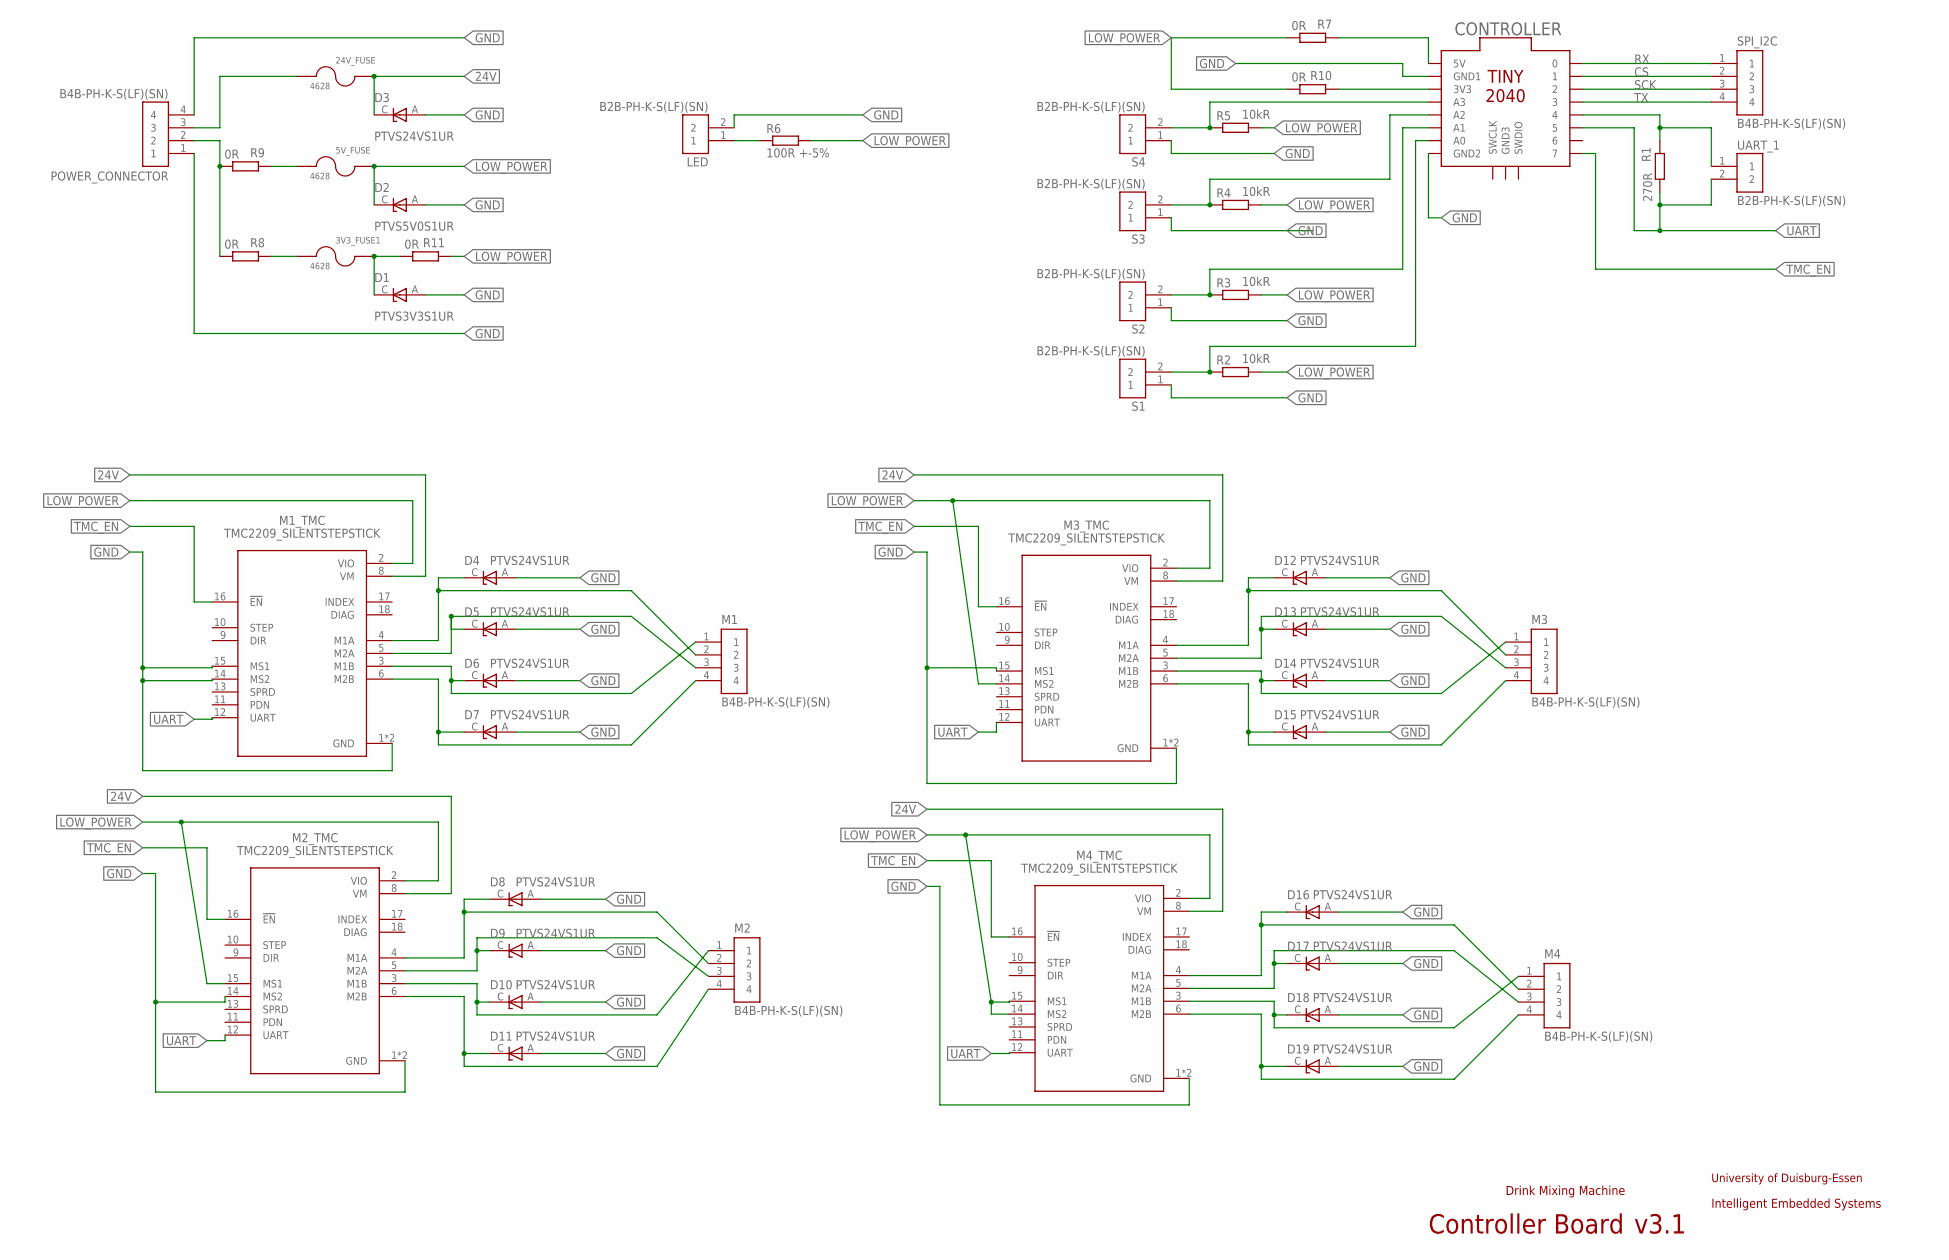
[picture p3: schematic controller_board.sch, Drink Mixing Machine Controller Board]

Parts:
3V3_FUSE1, 5V_FUSE, 24V_FUSE: 4628; FUSE_4628
CONTROLLER: TINY2040_HEADER
D1: PTVS3V3S1UR; TVS_PTVS3V3S1UR
D2: PTVS5V0S1UR; TVS_PTVS5V0S1UR
D3, D4, D5, D6, D7, D8, D9, D10, D11, D12, D13, D14, D15, D16, D17, D18, D19: PTVS24VS1UR; TVS_PTVS24VS1UR
LED: B2B-PH-K-S(LF)(SN); JST_B2B-PH-K-S(LF)(SN)
M1, M2, M3, M4: B4B-PH-K-S(LF)(SN); JST_B4B-PH-K-S(LF)(SN)
M1_TMC, M2_TMC, M3_TMC, M4_TMC: TMC2209_SILENTSTEPSTICK; MODULE_TMC2209_SILENTSTEPSTICK
POWER_CONNECTOR: B4B-PH-K-S(LF)(SN); JST_B4B-PH-K-S(LF)(SN)
R1: 270R; R0805
R2, R3, R4, R5: 10kR; R0805
R6: 100R +-5%; R0805
R7, R8, R9, R10, R11: 0R; R0805
S1, S2, S3, S4: B2B-PH-K-S(LF)(SN); JST_B2B-PH-K-S(LF)(SN)
SPI_I2C: B4B-PH-K-S(LF)(SN); JST_B4B-PH-K-S(LF)(SN)
UART_1: B2B-PH-K-S(LF)(SN); JST_B2B-PH-K-S(LF)(SN)

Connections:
3V3: 3V3_FUSE1.2, D1.C, R11.2
24V: 24V_FUSE.2, D3.C, M1_TMC.8 (VM), M2_TMC.8 (VM), M3_TMC.8 (VM), M4_TMC.8 (VM)
A0: CONTROLLER.A0, R2.1, S1.2
A1: CONTROLLER.A1, R3.1, S2.2
A2: CONTROLLER.A2, R4.1, S3.2
CS: CONTROLLER.1, SPI_I2C.2
GND: CONTROLLER.GND1, CONTROLLER.GND2, D1.A, D2.A, D3.A, D4.A, D5.A, D6.A, D7.A, D8.A, D9.A, D10.A, D11.A, D12.A, D13.A, D14.A, D15.A, D16.A, D17.A, D18.A, D19.A, LED.2, M1_TMC.1 (GND), M1_TMC.7 (GND), M1_TMC.14 (MS2), M1_TMC.15 (MS1), M2_TMC.1 (GND), M2_TMC.7 (GND), M2_TMC.14 (MS2), M3_TMC.1 (GND), M3_TMC.7 (GND), M3_TMC.15 (MS1), M4_TMC.1 (GND), M4_TMC.7 (GND), POWER_CONNECTOR.1, POWER_CONNECTOR.4, S1.1, S2.1, S3.1, S4.1
LOW_POWER: 5V_FUSE.2, D2.C, M1_TMC.2 (VIO), M2_TMC.2 (VIO), M2_TMC.15 (MS1), M3_TMC.2 (VIO), M3_TMC.14 (MS2), M4_TMC.2 (VIO), M4_TMC.14 (MS2), M4_TMC.15 (MS1), R2.2, R3.2, R4.2, R5.2, R6.2, R7.2, R10.2, R11.1
unnamed: POWER_CONNECTOR.2, R8.2, R9.2
unnamed: D4.C, M1.2, M1_TMC.4 (M1A)
unnamed: 5V_FUSE.1, R9.1
unnamed: D6.C, M1.1, M1_TMC.3 (M1B)
unnamed: D8.C, M2.2, M2_TMC.4 (M1A)
unnamed: D11.C, M2.4, M2_TMC.6 (M2B)
unnamed: D9.C, M2.3, M2_TMC.5 (M2A)
unnamed: D10.C, M2.1, M2_TMC.3 (M1B)
unnamed: D12.C, M3.2, M3_TMC.4 (M1A)
unnamed: D15.C, M3.4, M3_TMC.6 (M2B)
unnamed: D13.C, M3.3, M3_TMC.5 (M2A)
unnamed: D14.C, M3.1, M3_TMC.3 (M1B)
unnamed: D16.C, M4.2, M4_TMC.4 (M1A)
unnamed: D19.C, M4.4, M4_TMC.6 (M2B)
unnamed: D17.C, M4.3, M4_TMC.5 (M2A)
unnamed: D18.C, M4.1, M4_TMC.3 (M1B)
unnamed: LED.1, R6.1
unnamed: CONTROLLER.5V, R7.1
unnamed: D7.C, M1.4, M1_TMC.6 (M2B)
unnamed: CONTROLLER.4, R1.1, UART_1.1
unnamed: 3V3_FUSE1.1, R8.1
unnamed: 24V_FUSE.1, POWER_CONNECTOR.3
unnamed: CONTROLLER.3V3, R10.1
unnamed: CONTROLLER.A3, R5.1, S4.2
unnamed: D5.C, M1.3, M1_TMC.5 (M2A)
RX: CONTROLLER.0, SPI_I2C.1
SCK: CONTROLLER.2, SPI_I2C.3
TMC_EN: CONTROLLER.7, M1_TMC.16 (!EN), M2_TMC.16 (!EN), M3_TMC.16 (!EN), M4_TMC.16 (!EN)
TX: CONTROLLER.3, SPI_I2C.4
UART: CONTROLLER.5, M1_TMC.12 (UART), M2_TMC.12 (UART), M3_TMC.12 (UART), M4_TMC.12 (UART), R1.2, UART_1.2

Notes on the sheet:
Intelligent Embedded Systems
University of Duisburg-Essen
Drink Mixing Machine
Controller Board

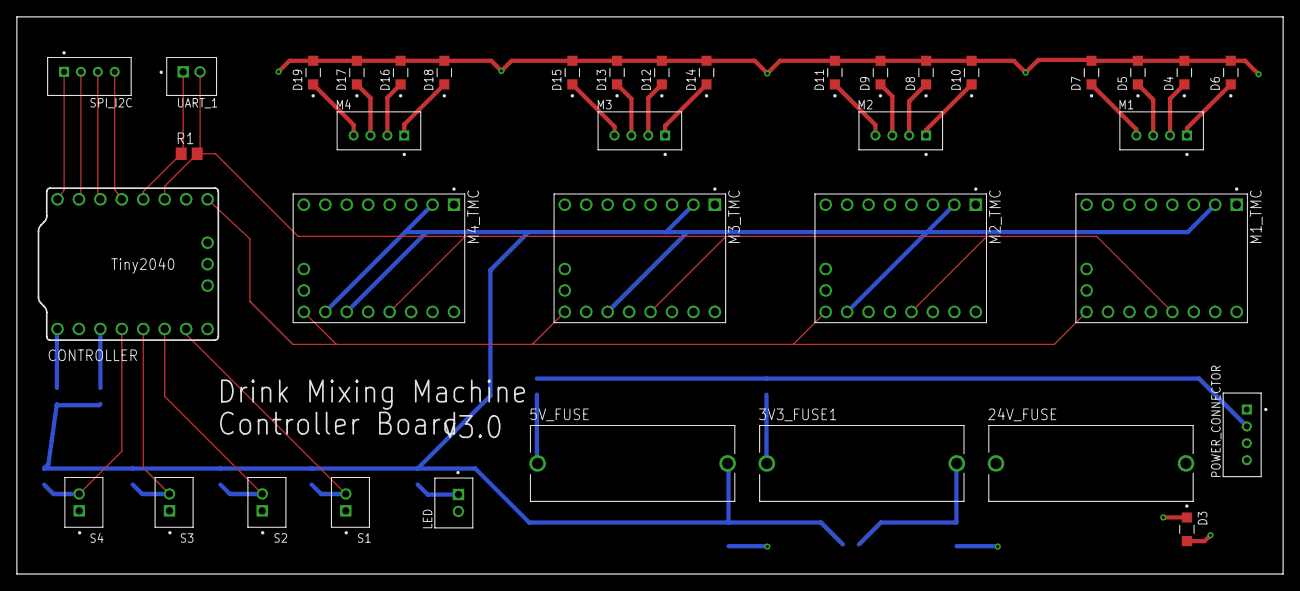
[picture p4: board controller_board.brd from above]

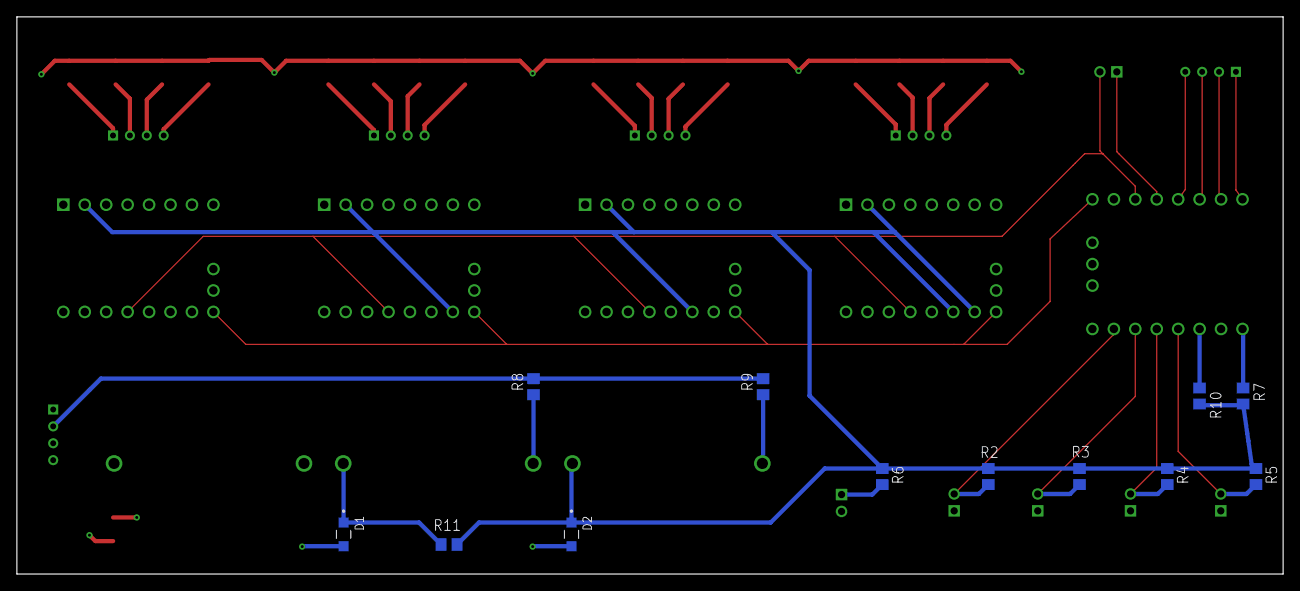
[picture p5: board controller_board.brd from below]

Board: 4 copper layers, 150.0 x 66.0 mm, 50 parts (12 on the bottom side), 38 nets.

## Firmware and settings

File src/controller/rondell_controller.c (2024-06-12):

#define SOURCE_FILE "RONDELL"

#include "com_protocol.h"
#include "common.h"
#include "dispenser.h"
#include "rondell.h"

#include "hardware/adc.h"
#include "hardware/watchdog.h"
#include "pico/stdlib.h" /// must be included -> sets clocks required for watchdog-timer!!

#include <stdio.h>
#include <string.h>

/* region VARIABLES/DEFINES */

#ifndef CONTROLLER_ID
#error "Controller ID must be defined!"
#endif

#define NUMBER_OF_DISPENSER 4
dispenser_t dispenser; /// Array containing the dispenser

#define INPUT_BUFFER_LEN 255 /// maximum count of allowed input length
size_t characterCounter;
char inputBuffer[INPUT_BUFFER_LEN];

bool dispenserInitialized = false;

/* endregion VARIABLES/DEFINES */

/* region HELPER FUNCTIONS */

/*
 * @param gpio[in] GPIO of the ADC (26-29)
 */
void initializeAdc(uint8_t gpio) {
    adc_init();
    adc_gpio_init(gpio);
    adc_select_input(gpio - 26);

    PRINT("Initialized ADC %u (GPIO %u)", gpio - 26, gpio);
}

void initDispenser(void) {
    PRINT("activate motor");
    initializeAndActivateMotorsEnablePin(); // Enable TMC2209 drivers

    PRINT("init rondell");
    createRondell(MOTOR_ADDRESS_2);

    PRINT("init dispenser");
    dispenserCreate(&dispenser, MOTOR_ADDRESS_0, 4, true);

    dispenserInitialized = true;
}

void processMessage(char *message, size_t messageLength) {
    PRINT("Process message len: %u", messageLength);
    PRINT("Message: %s", message);

    if (strstr("i", message) != NULL) {
        PRINT_COMMAND("%s", CONTROLLER_ID);
        if (dispenserInitialized) {
            PRINT_COMMAND("CALIBRATED");
        }
        return;
    }

    for (uint8_t i = 0; i < NUMBER_OF_DISPENSER; ++i) {
        uint32_t dispenserHaltTime = parseInputString(&message);
        if (dispenserHaltTime > 0) {
            dispenser.haltTime = dispenserHaltTime;
            watchdog_update();
            moveToDispenserWithId(i);
            do {
                watchdog_update();
                dispenserExecuteNextState(&dispenser);
            } while (!dispenserInSleepState(&dispenser));
        }
    }
}

_Noreturn void run() {
    resetMessageBuffer(inputBuffer, INPUT_BUFFER_LEN, &characterCounter);

//    watchdog_enable(60 * 1000, true);

    while (true) {
        // watchdog update needs to be performed frequent, otherwise the device will crash
        watchdog_update();

        /* region Handle received character */
        int input = getchar_timeout_us(3 * 1000000);

        PRINT("Start Processing Input!");
        if (input == PICO_ERROR_TIMEOUT) {
            PRINT("No command received! Timeout reached.");
            continue;
        }
        PRINT("No timeout reached!");

        if (!isAllowedCharacter(input)) {
            PRINT("Received '%c' which is not allowed. It will be ignored", input);
            continue;
        }
        PRINT("Received valid character");

        if (isMessageToLong(characterCounter, INPUT_BUFFER_LEN)) {
            resetMessageBuffer(inputBuffer, INPUT_BUFFER_LEN, &characterCounter);
            PRINT("Input too long! Flushed buffer.");
            continue;
        }
        PRINT("Message Buffer not full!");

        if (isLineEnd(input)) {
            handleMessage(inputBuffer, INPUT_BUFFER_LEN, &characterCounter);
            PRINT_COMMAND("READY");
            continue;
        }
        PRINT("Message end not reached!");

        storeCharacter(inputBuffer, &characterCounter, input);

        /* endregion handle received character */
    }
}

/* endregion HELPER FUNCTIONS */

int main() {
    initIO(false);
    initializeAdc(27);
    initDispenser();

    run();
}

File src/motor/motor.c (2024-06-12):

#define SOURCE_FILE "MOTOR"

#include "motor.h"
#include "common.h"

#include <hardware/gpio.h>
#include <pico/time.h>

#ifndef SERIAL_UART
#error "SERIAL_UART instance needs to be defined!"
#endif

#define MOTOR_ENABLE_PINT 7

#ifndef MOTOR_UP_SPEED
#error "MOTOR_UP_SPEED not defined"
#endif
#ifndef MOTOR_UP_SPEED_SLOW
#define MOTOR_UP_SPEED_SLOW 100000
#endif
#ifndef MOTOR_DOWN_SPEED
#error "MOTOR_DOWN_SPEED not defined"
#endif

#define MOTOR_UP_SPEED_SLOW 100000

static uint16_t torque = 0;
static uint8_t enablePin;
Motor_t motors[4];

void initializeAndActivateMotorsEnablePin() {
    enablePin = MOTOR_ENABLE_PINT;
    gpio_init(enablePin);
    gpio_set_dir(enablePin, GPIO_OUT);
    gpio_pull_down(enablePin);
}

void setUpMotor(Motor_t *motor, SerialAddress_t address) {
    TMC2209_setupByMotor(&motor->tmc2209, address);

    while (!TMC2209_isSetupAndCommunicating(&motor->tmc2209)) {
        if (TMC2209_disabledByInputPin(&motor->tmc2209)) {
            PRINT("Setup: Stepper driver with address %u DISABLED by input pin!", address);
        }
        PRINT("Setup: Stepper driver with address %u NOT communicating and setup!", address);
        TMC2209_setupByMotor(&motor->tmc2209, address);
        sleep_ms(500);
    }

    PRINT("Setup: Stepper driver with address %u communicating and setup!", address);
    TMC2209_setRunCurrent(&motor->tmc2209, 100);
    TMC2209_setHoldCurrent(&motor->tmc2209, 50);
    TMC2209_enable(&motor->tmc2209);
    TMC2209_moveAtVelocity(&motor->tmc2209, 0);
}

bool motorIsCommunicating(motorAddress_t address) {
    Motor_t *motor = getMotor(address);
    return TMC2209_isSetupAndCommunicating(&motor->tmc2209);
}

Motor_t *getMotor(motorAddress_t address) {
    if (address >= 0 && address < 5) {
        return &motors[address];
    } else {
        PRINT("Didnt find motor");
        // Handle invalid motorNum
        return NULL;
    }
}

Motor_t createMotor(motorAddress_t address) {
    motors[address].address = (int)address;
    setUpMotor(&motors[address], (int)address);
    return motors[address];
}

uint16_t motorGetTorque(motorAddress_t address) {
    Motor_t *motor = getMotor(address);
    torque = TMC2209_getStallGuardResult(&motor->tmc2209);
    return torque;
}

static void moveMotor(Motor_t *motor, int32_t speed) {
    TMC2209_moveAtVelocity(&motor->tmc2209, speed);
}
void moveMotorUp(motorAddress_t address) {
    Motor_t *motor = getMotor(address);
    moveMotor(motor, MOTOR_UP_SPEED);
}
void moveMotorUpSlowSpeed(motorAddress_t address) {
    Motor_t *motor = getMotor(address);
    moveMotor(motor, MOTOR_UP_SPEED_SLOW);
}
void moveMotorDown(motorAddress_t address) {
    Motor_t *motor = getMotor(address);
    moveMotor(motor, (-1) * MOTOR_DOWN_SPEED);
}
void stopMotor(motorAddress_t address) {
    Motor_t *motor = getMotor(address);
    moveMotor(motor, 0);
}

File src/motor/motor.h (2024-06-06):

#ifndef SIEGMA_MOTOR_H
#define SIEGMA_MOTOR_H

#include "tmc2209.h"
#include <stdint.h>


/// struct containing information (pins, stepper driver, direction, Serial address) for a motor
typedef struct Motor {
    TMC2209_t tmc2209;
    SerialAddress_t address;
    int direction;
} Motor_t;

typedef enum motorAddress {
    MOTOR_ADDRESS_0 = 0,
    MOTOR_ADDRESS_1 = 1,
    MOTOR_ADDRESS_2 = 2,
    MOTOR_ADDRESS_3 = 3,
} motorAddress_t;

void initializeAndActivateMotorsEnablePin();

/*! initializes a new motor
 *
 * @param motor   the new initialized motor
 * @param address serial address of the motor (for more information:
 * https://github.com/janelia-arduino/TMC2209)
 * @param uart    uart pins to be used
 */
void setUpMotor(Motor_t *motor, SerialAddress_t address); // serialUart_t uart

/*! Move the motor up
 *
 * @param motor motor to be moved
 */
/*void moveMotorUp(Motor_t *motor);*/
void moveMotorUp(motorAddress_t address);

/*! Move the motor up to Stop under the Dispenser
 *
 * @param motor motor to be moved
 */
void moveMotorUpSlowSpeed(motorAddress_t address);

/*! Move the motor down
 *
 * @param motor motor to be moved
 */
/*void moveMotorDown(Motor_t *motor);*/
void moveMotorDown(motorAddress_t address);

/*! Stop the motor
 *
 * @param motor motor to be stopped
 */
/*void stopMotor(Motor_t *motor);*/
void stopMotor(motorAddress_t address);

/*! Create a new motor and initialize its pins
 *
 * @param address serial address of the stepper driver (for more information:
 * https://github.com/janelia-arduino/TMC2209)
 * @param uart    uart pins to be used
 * @return        motor struct of the new motor
 */
Motor_t createMotor(motorAddress_t address);

/*! Check if the motor is capable of communication over uart
 *
 * @param motor motor to be checked
 * @return      true if the motor communicates, otherwise false
 */
bool motorIsCommunicating(motorAddress_t address);

Motor_t *getMotor(motorAddress_t address);

uint16_t motorGetTorque(motorAddress_t address);

#endif // SIEGMA_MOTOR_H

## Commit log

2023-04-19 fix build: fixed build files / includes
    [dispenser.c, limitSwitch.c, limitSwitch.h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]
2023-04-21 refactor(motor):
    refactor motor library for improved readability
2023-04-22 refactor(serialUart):
    refactor serial UART library for improved readability
2023-04-26 chore(common): add PRINT_COMMAND makro
    Add special makro for commands required for the implementation and communication with the Pi
2023-04-26 style(debug-print): apply print makros
2023-04-27 fix(main)(fix dispensing liquids):
    Functions was wrong due to flase refactoring
    [dispenser.c]
2023-04-28 fix(dispenser): replaced PRINT with PRINT_DEBUG
    [dispenser.c]
2023-05-09 perf(main): add watchdog timer
    add watchdog time of 15s
    improved readability by extracting code into functions
    declared function prototypes for internal functions
2023-05-14 refactor(motor): update dependencies
2023-05-23 fix(watchdog): fix implementation so that watchdog is working correctly
    [dispenser.c, rondell_controller.c]
2023-06-04 test(dispenser rigth side): Changed speed to 150000 and adjusted Steps. Added missing breaks.
    [motor.h]
2023-06-13 fix(rondell): add second watchdog timer reset
    [rondell_controller.c]
2023-06-29 fix(Dispenser-Speed): Calculation of stepsPerSecond
    [dispenser.c, motor.h]
2023-07-05 build(pico-sdk): update pico-sdk to latest release
2023-07-05 test(dispenser): fix integration for dispeneser
    [dispenser.c]
2023-07-05 fix(rondell): reduce motor speed of rondell
    required due to the fact,
    that the sensor is not fast enough otherwise
    [motor.h, rondell.c, rondell_controller.c]
2023-07-07 feat(torqueRecognition): Added functions to tmc2209.c
2023-07-07 feat(torqueRecognition): Torque Measuring does work
2023-07-10 fix(Speed of Dispenser): Adjust speed of Dispenser
    [motor.h]
2023-10-24 chore(PCB): moved old files to subfolder
    [Drill_PTH_Through.DRL, Drill_PTH_Through_Via.DRL, Gerber_BoardOutlineLayer.GKO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]
2023-10-24 doc(PCB): add new board schematics (AUTODESK EAGLE)
    [controller_board.brd, controller_board.sch]
2023-11-05 chore(pcb): improve schematics
    [controller_board.brd, controller_board.sch]
2023-11-06 feat(pcb): add ESD protection
    [controller_board.brd, controller_board.sch]
2023-11-07 feat(pcb): add proper PCB layout
    [controller_board.brd, controller_board.sch]
2023-11-07 Measuring torque - Logic of processMessage, time consumption optimized
2023-11-07 Measuring torque - Logic of processMessage, time consumption optimized. Removed testing code
2023-11-07 refactor(Dispenser): When limit switch is closed in initialization, motor does not move
2023-11-08 feat(pcb): add wires
    [controller_board.brd, controller_board.sch]
2023-11-13 feat(pcb): add 3V3 circuit
    [controller_board.brd, controller_board.sch]
2023-11-14 feat(pcb): replace ESD protection with TVS-Diode
    [controller_board.brd, controller_board.sch]
2023-11-16 #41 perf(torque) measure torque's value more frequently.
2023-11-16 feat(pcb): add TMC enable pin
    [controller_board.brd, controller_board.sch]
2023-11-16 chore(pcb): rename folder to correct version
    [Drill_PTH_Through.DRL, Drill_PTH_Through_Via.DRL, Gerber_BoardOutlineLayer.GKO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]
2023-11-17 fix(pcb): fix tiny2040 library
    [controller_board.brd, controller_board.sch]
2023-11-17 chore(pcb): add libraries
2023-12-12 docs(pcb): added gerber files for JCLPCB 4-layer
    Added Eagle generated gerber files based on jclpcb provided CAM file
    -> added too!
    [controller_board_Legend_Bot.GBO, controller_board_Legend_Top.GTO, controller_board_Paste_Bot.GBP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]
2023-12-17 test(unit test): fix and improve the coverage of unit test
    [gpio.h, serialUART.h, tmc2209.c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]
2023-12-18 fix(integrationTest_dispenser.c): can be build for now.
    [dispenser.c]
2023-12-18 fix(unit test dispenser): fix the parameter uart used by dispenserCreate
2023-12-19 fix(unit test): fixed two multi-definition errors
    [gpio.h, tmc2209.c, tmc2209.h]
2023-12-19 fix(unit test): naming, undeclared errors
    [serialUART.h, tmc2209.c, tmc2209.h]
2023-12-22 docs(pcb). add part list with order links
    [PCB v3.0 Parts.ods]
2024-01-01 feat(dispenser): Added torque detection in resetDispenserPosition and downstate
    [dispenser.c, motor.c, motor.h]
2024-01-01 feat(tmc2209): Added function for Motor-Position
2024-01-08 bug(main): function to other position
    [dispenser.c]
2024-01-14 bug(main-Code): Moved function to other position
    [rondell_controller.c]
2024-01-23 perf(dispenser): change torque to dispenser->torque, reduce the sleep time in TMC2209_read, measure torque more frequently.
2024-02-02 refactor(Motor-GPIO): With the new PCB only one Enable/Disable Pin is available for all Motors
2024-02-02 refactor(Motor-Enable): Some more refactoring for the enable pin
2024-02-03 fix(pico-sdk): set referenced versio to last release!!
2024-02-05 fix(limitswitch) test(adc): fix limitswitch/adc gpio asscoiations
    [integrationTest_adc.c, limitSwitch.h]
2024-02-06 style(motor): apply formatting
2024-02-06 test(motor): fix TMC initialization
    [integrationTest_motor.c]
2024-02-06 fix(schmatic): update UART resistor value
    [controller_board.brd, controller_board.sch]
2024-02-13 fix(unit-test): rewrite the dummy torque value, fixed failing unit-test_dispenser.
    [tmc2209.c]
2024-02-20 fix controller by moving motorsenablepin before dispenser
2024-02-20 fix controller by moving the MotorsEnablePin before dispenser init
2024-02-20 move motor check out of do while
2024-02-20 move motor check out of do while--right_controller
2024-02-27 perf(dispenser): change time to wait TMC switch off output to 21us and add sleep 1ms in topState to approximate halt time.
2024-02-28 fix(motor): build(cmake): pass motor speed via CMake target
    [motor.c, motor.h, rondell.c]
2024-02-29 fix(dispenser): fix motor init
    [integrationTest_adc.c, motor.c, rondell_controller.c]
2024-02-29 test(dispenser): add velocity
2024-02-29 fix(dispenser): add more accurate halt time back and remove redundant TMC_moveAtVelocity call.
    [motor.c]
2024-03-01 fix datatype of haltime and add some comments.
    [dispenser.c, tmc2209.c]
2024-03-01 remove commented out code in motor.
2024-06-06 ci(cmake): replace git submodules with cmake fetch
    [dispenser.c, integrationTest_adc.c, integrationTest_motor.c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]
2024-06-06 fix(com-protocol): extraxt communication protocol
    [rondell_controller.c]
2024-06-10 fix(dispenser): enable disabling contact state for rondell
    [dispenser.c, rondell_controller.c]
2024-06-12 fix(controller): fixes for demo
    [dispenser.c, integrationTest_adc.c, motor.c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]
